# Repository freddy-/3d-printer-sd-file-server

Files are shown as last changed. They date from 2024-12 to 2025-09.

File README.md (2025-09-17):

# ESP8266 SD Card File Server For 3D Printer

This project mimics the file upload endpoint of OctoPrint allowing to send gcode from prusa slicer and saving direct to SD card.

It is based on ardyesp/ESPWebDAV and FYSETC/ESPWebDAV.
 
SD card is shared between ESP8266 (SPI) and 3d printer (SDIO) running Marlin firmware with a custom change. 

The ESP8266 control the SD Card detection pin from the 3D Printer board. When it receive a file upload it simulate a SD card removal from the 3D Printer and then initialize the SD Card in SPI mode. When the file upload is done it performs a power cycle of the SD Card, otherwise the SD Card wont work in SDIO mode.

This change in Marlin allow the SDIO lines from the SD card to be shared with the ESP8266. When the card is removed from the 3D Printer Marlin detects and disable the SDIO hardware and set these pins to input.

### 3D Printer
The tests were made using a Kingroon KP3S. This printer have a MakerBase Robin Nano clone board with a connector for a external SD board.

### Firmware update
Firmware update can be done via browser through url `<esp-ip>/update`

### Dependencies
- [ESP8266 Arduino](https://github.com/esp8266/Arduino)  version 3.1.2

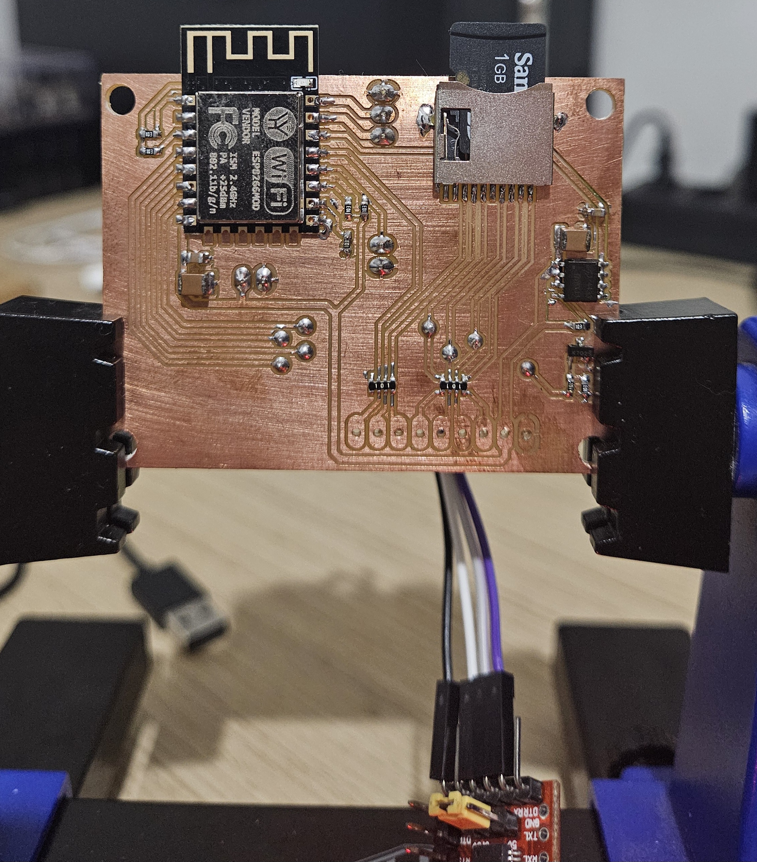
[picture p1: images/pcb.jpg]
pcb


<div style="display: flex;">
  <a href="images/printer1.jpg">
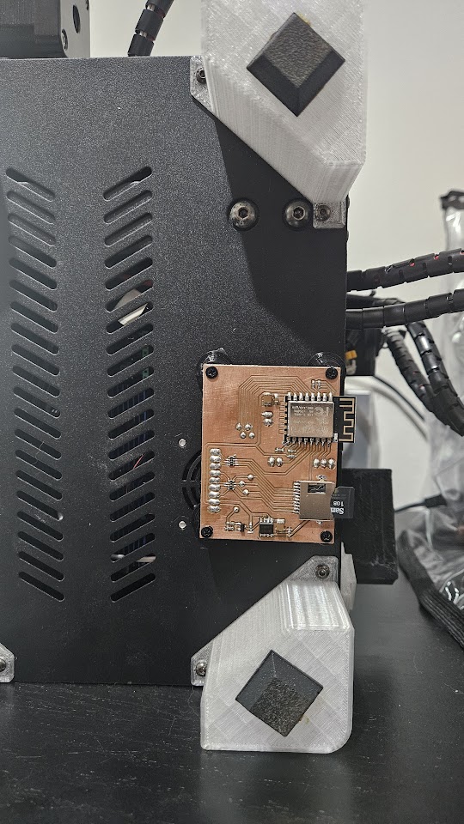
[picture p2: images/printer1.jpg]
    
  </a>
  <a href="images/printer2.jpg">
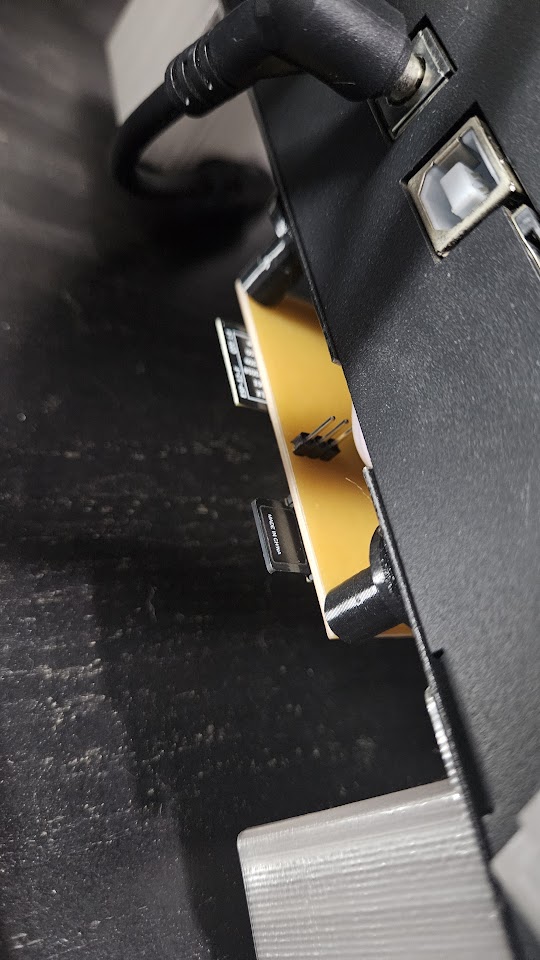
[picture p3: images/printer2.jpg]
    
  </a>
</div>

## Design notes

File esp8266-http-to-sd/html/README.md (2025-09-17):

# Convert HTML to C Array

This is based in the [ESP8266 FSBrowser](https://github.com/esp8266/Arduino/tree/master/libraries/ESP8266WebServer/examples/FSBrowser) example.

To convert a HTML file into a minified C Array run this command with the html file name without the `.html`:

```bash
./convert_html_to_c_header.sh index
```

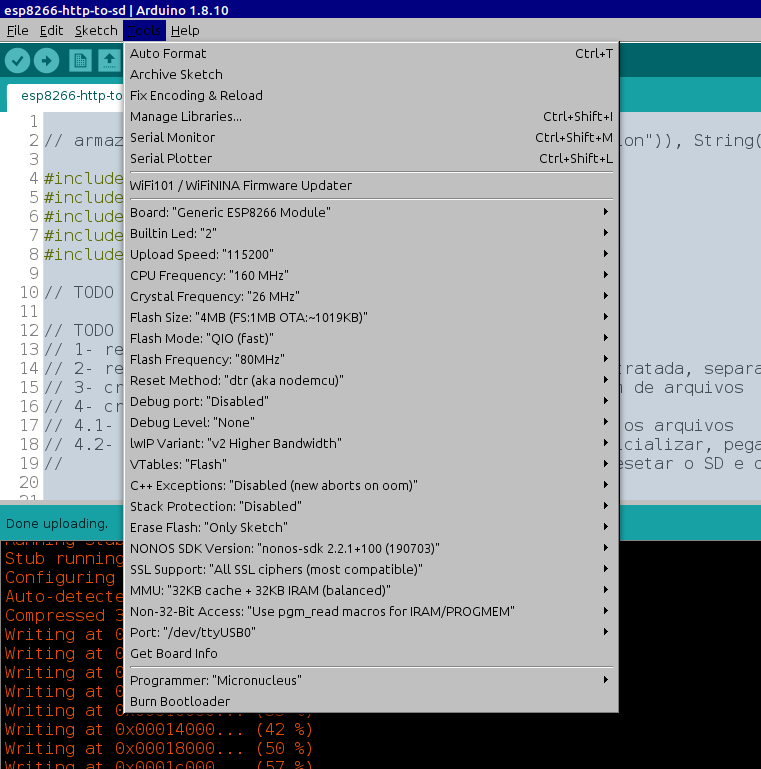
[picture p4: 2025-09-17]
esp8266-http-to-sd/arduino-config.png

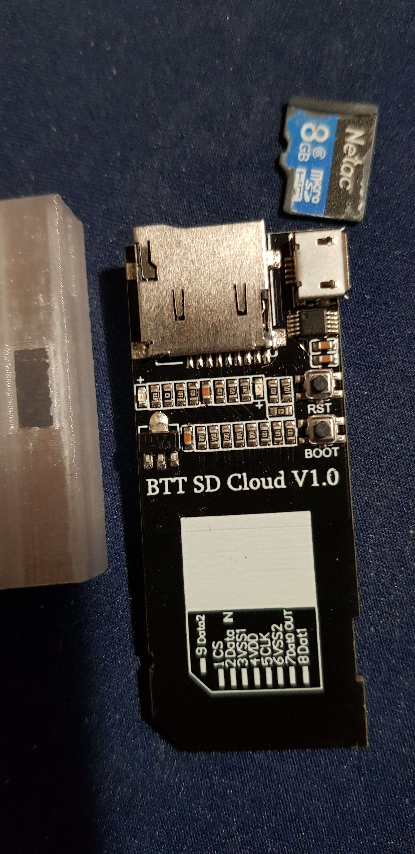
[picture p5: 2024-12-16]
esp8266-http-to-sd/99077462-14074700-25bd-11eb-9805-0963f63b4c84.jpg

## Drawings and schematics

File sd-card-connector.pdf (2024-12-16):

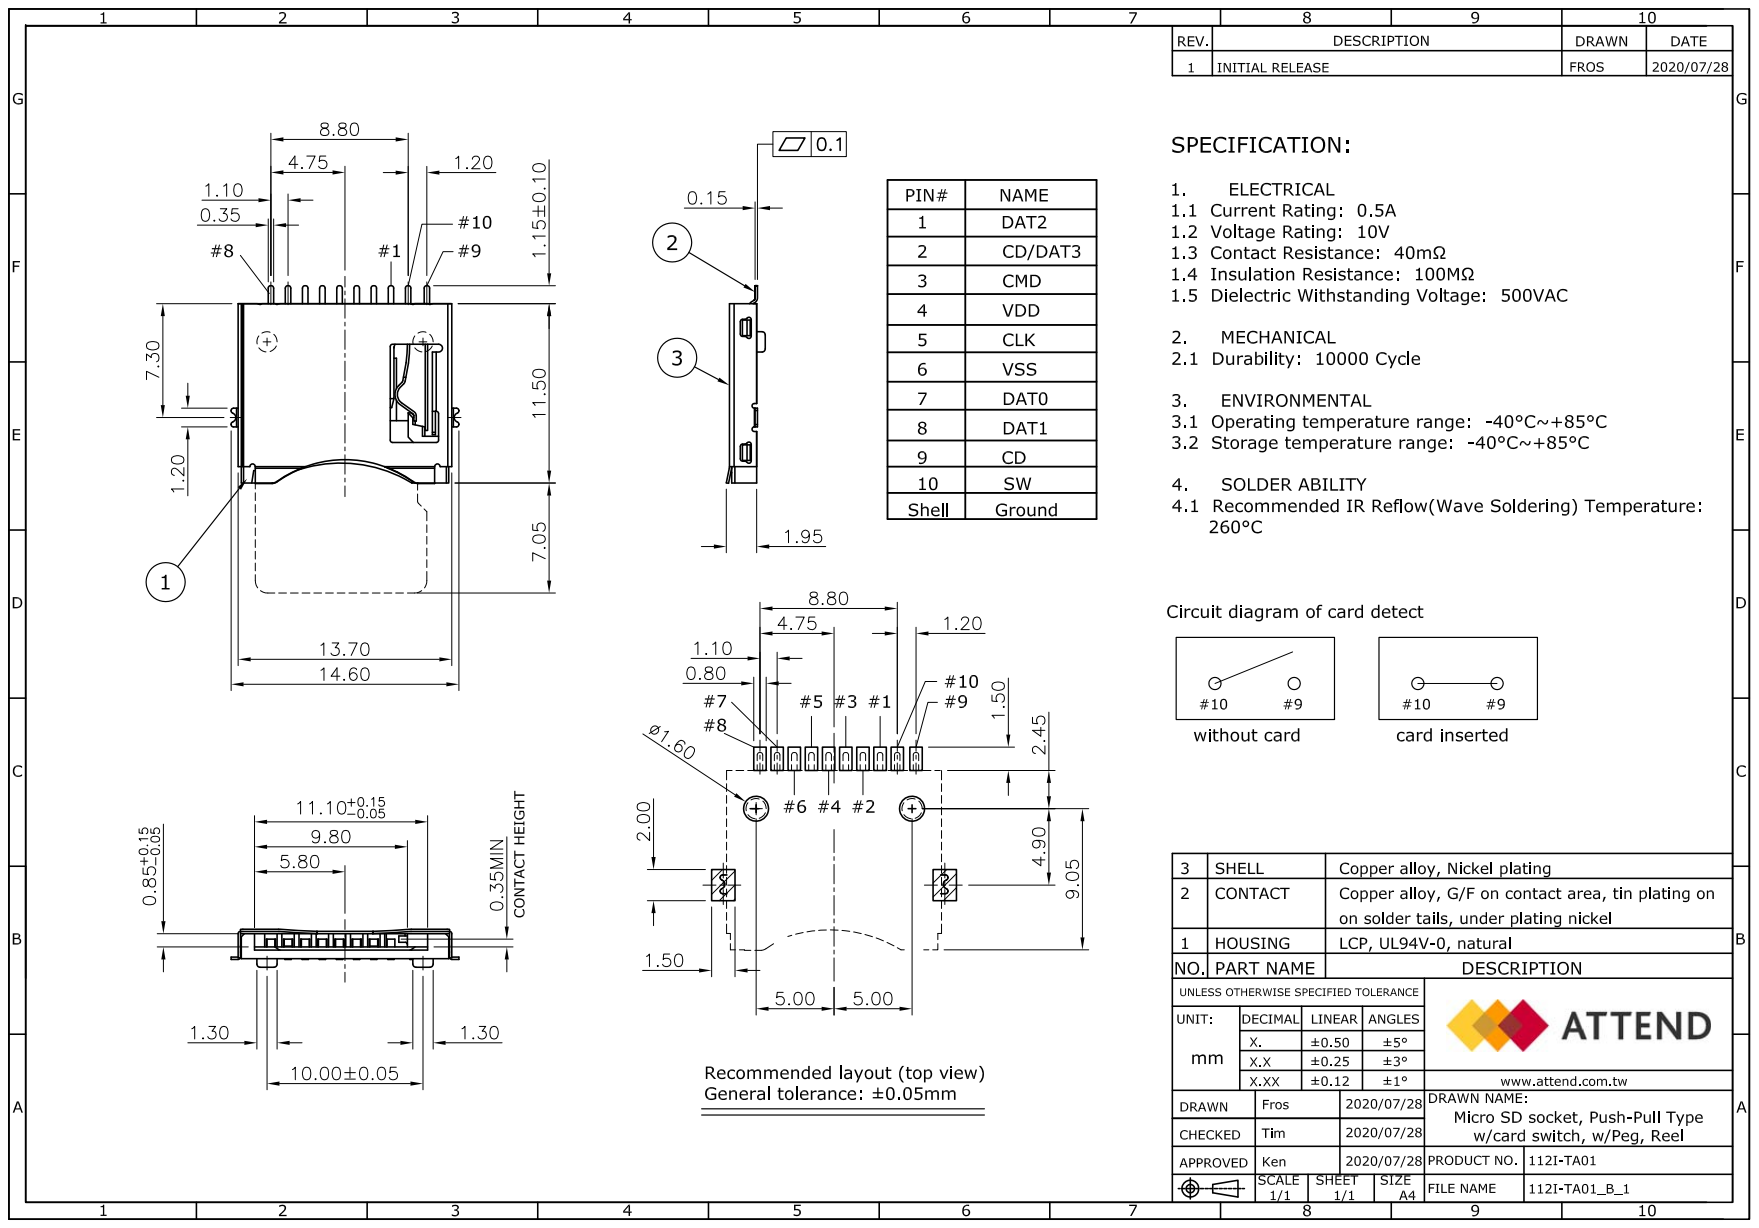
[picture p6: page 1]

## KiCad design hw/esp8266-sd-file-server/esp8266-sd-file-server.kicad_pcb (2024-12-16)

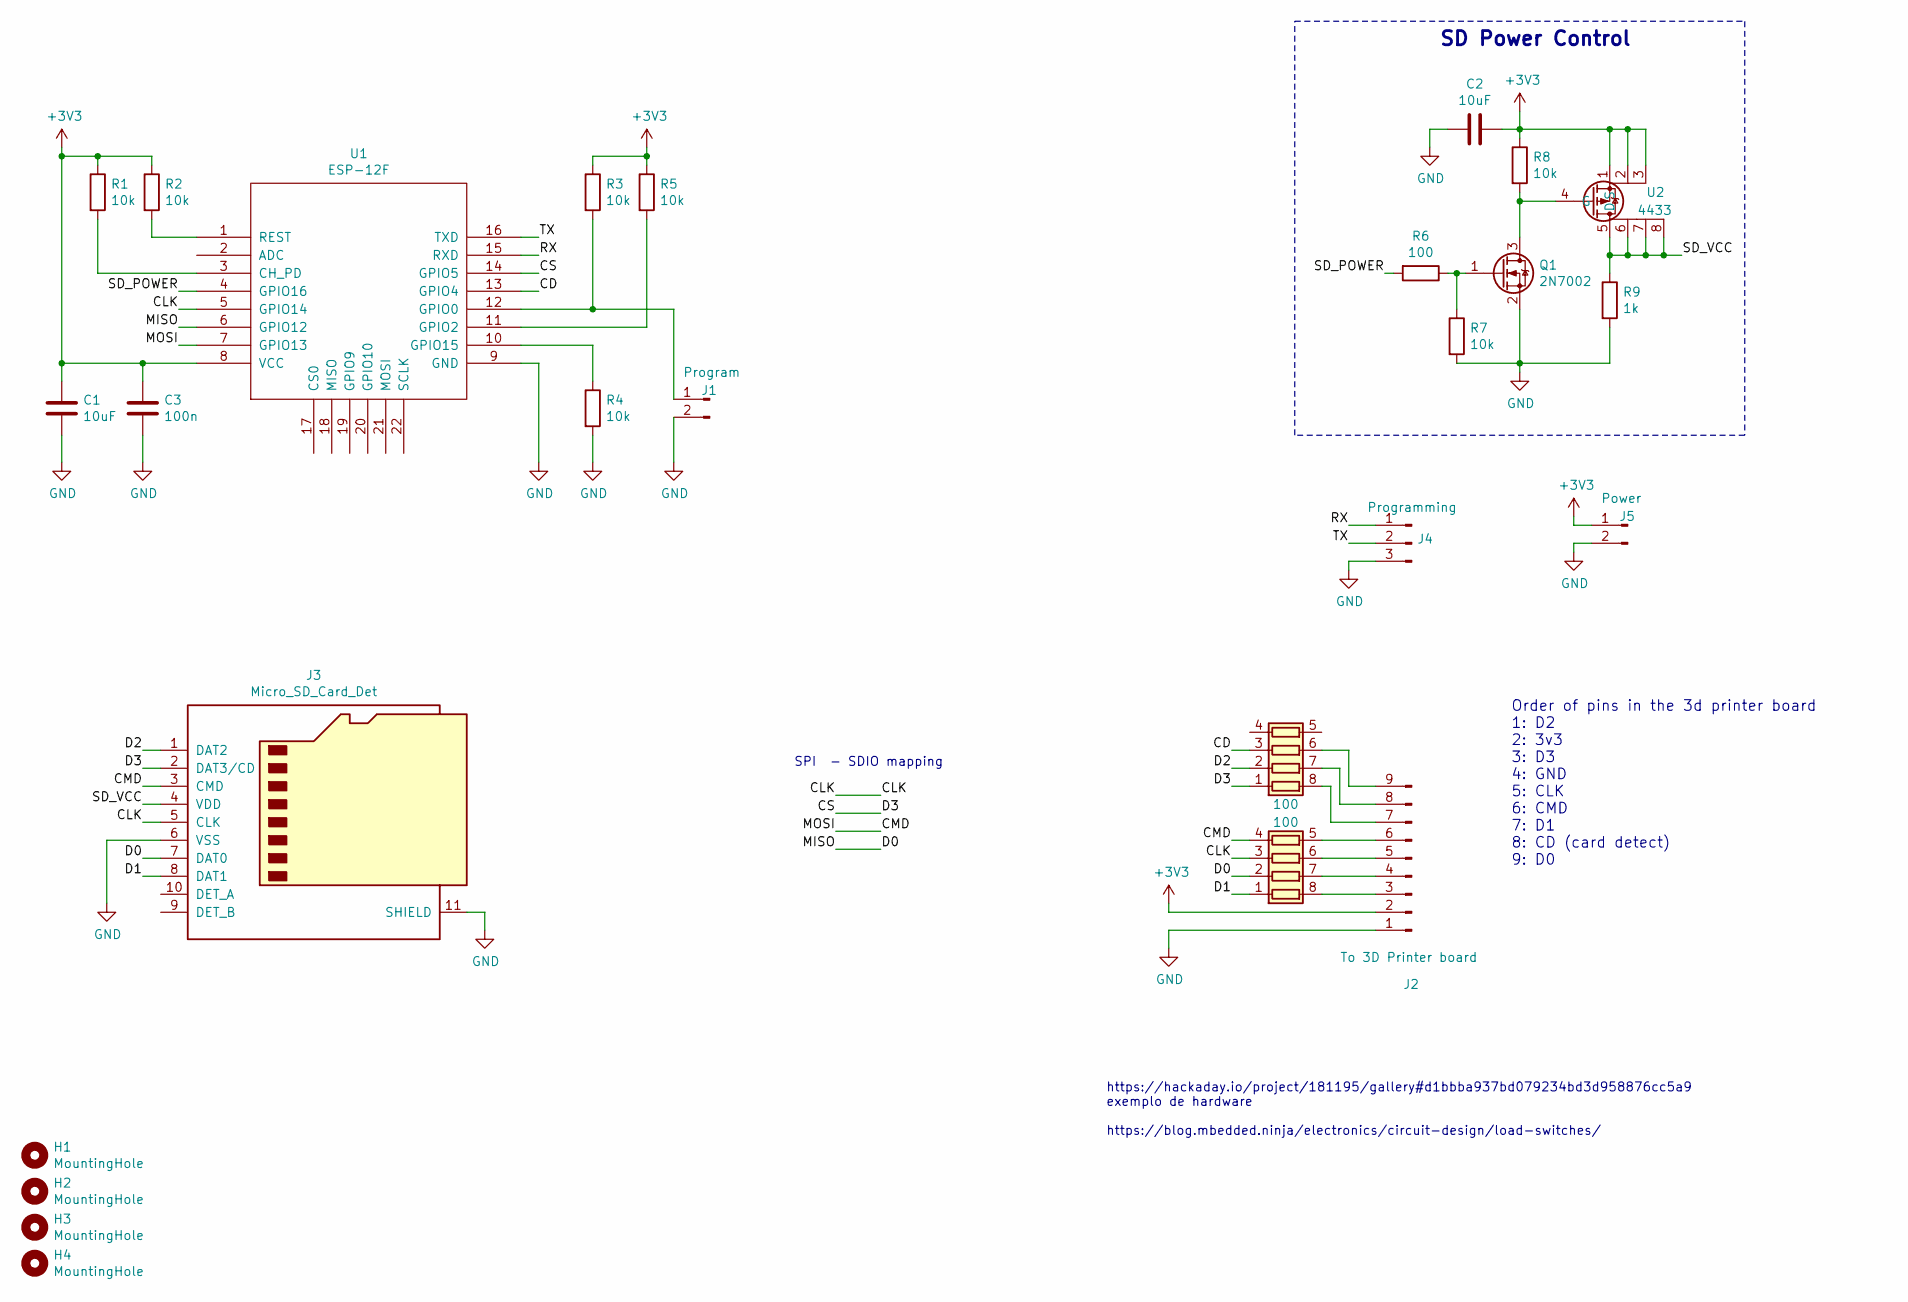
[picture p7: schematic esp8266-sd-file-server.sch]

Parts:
C1, C2: 10uF; C_1210_3225Metric_Pad1.42x2.65mm_HandSolder
C3: 100n; C_0805_2012Metric_Pad1.15x1.40mm_HandSolder
H1, H2, H3, H4: MountingHole; MountingHole_3mm
J1: Program; PinHeader_1x02_P2.54mm_Vertical
J2: To 3D Printer board; PinHeader_1x09_P2.54mm_Vertical
J3: Micro_SD_Card_Det; micro_sd
J4: Programming; PinHeader_1x03_P2.54mm_Vertical
J5: Power; PinHeader_1x02_P2.54mm_Vertical
Q1: 2N7002; SOT-23
R1, R2, R3, R4, R5, R7, R8: 10k; R_0603_1608Metric_Pad1.05x0.95mm_HandSolder
R6: 100; R_0603_1608Metric_Pad1.05x0.95mm_HandSolder
R9: 1k; R_0603_1608Metric_Pad1.05x0.95mm_HandSolder
RN1, RN2: 100; R_Array_Convex_4x0603
U1: ESP-12F; ESP-12E_SMD
U2: 4433; SOIC-8_3.9x4.9mm_P1.27mm

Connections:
+3V3: C1.2, C2.1, C3.2, J2.2, J5.1, R1.1, R2.1, R3.1, R5.1, R8.1, U1.8 (VCC), U2.1 (S), U2.2, U2.3
/CD: RN2.3 (R3.1), U1.13 (GPIO4)
/CLK: J3.5 (CLK), RN1.3 (R3.1), U1.5 (GPIO14)
/CMD: J3.3 (CMD), RN1.4 (R4.1), U1.7 (GPIO13)
/CS: J3.2 (DAT3/CD), RN2.1 (R1.1), U1.14 (GPIO5)
/D0: J3.7 (DAT0), RN1.2 (R2.1), U1.6 (GPIO12)
/D1: J3.8 (DAT1), RN1.1 (R1.1)
/D2: J3.1 (DAT2), RN2.2 (R2.1)
/RX: J4.1, U1.15 (RXD)
/SD_POWER: R6.2, U1.4 (GPIO16)
/SD_VCC: J3.4 (VDD), R9.1, U2.5 (D), U2.6, U2.7, U2.8
/TX: J4.2, U1.16 (TXD)
GND: C1.1, C2.2, C3.1, J1.2, J2.1, J3.6 (VSS), J3.11 (SHIELD), J4.3, J5.2, Q1.2 (S), R4.2, R7.2, R9.2, U1.9 (GND)
unnamed: J1.1, R3.2, U1.12 (GPIO0)
unnamed: J2.3, RN1.8 (R1.2)
unnamed: J2.4, RN1.7 (R2.2)
unnamed: J2.5, RN1.6 (R3.2)
unnamed: J2.6, RN1.5 (R4.2)
unnamed: J2.7, RN2.8 (R1.2)
unnamed: J2.8, RN2.7 (R2.2)
unnamed: J2.9, RN2.6 (R3.2)
unnamed: Q1.1 (G), R6.1, R7.1
unnamed: Q1.3 (D), R8.2, U2.4 (G)
unnamed: R1.2, U1.3 (CH_PD)
unnamed: R2.2, U1.1 (REST)
unnamed: R4.1, U1.10 (GPIO15)
unnamed: R5.2, U1.11 (GPIO2)

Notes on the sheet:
SD Power Control
https://hackaday.io/project/181195/gallery#d1bbba937bd079234bd3d958876cc5a9 exemplo de hardware https://blog.mbedded.ninja/electronics/circuit-design/load-switches/
SPI - SDIO mapping
Order of pins in the 3d printer board 1: D2 2: 3v3 3: D3 4: GND 5: CLK 6: CMD 7: D1 8: CD (card detect) 9: D0

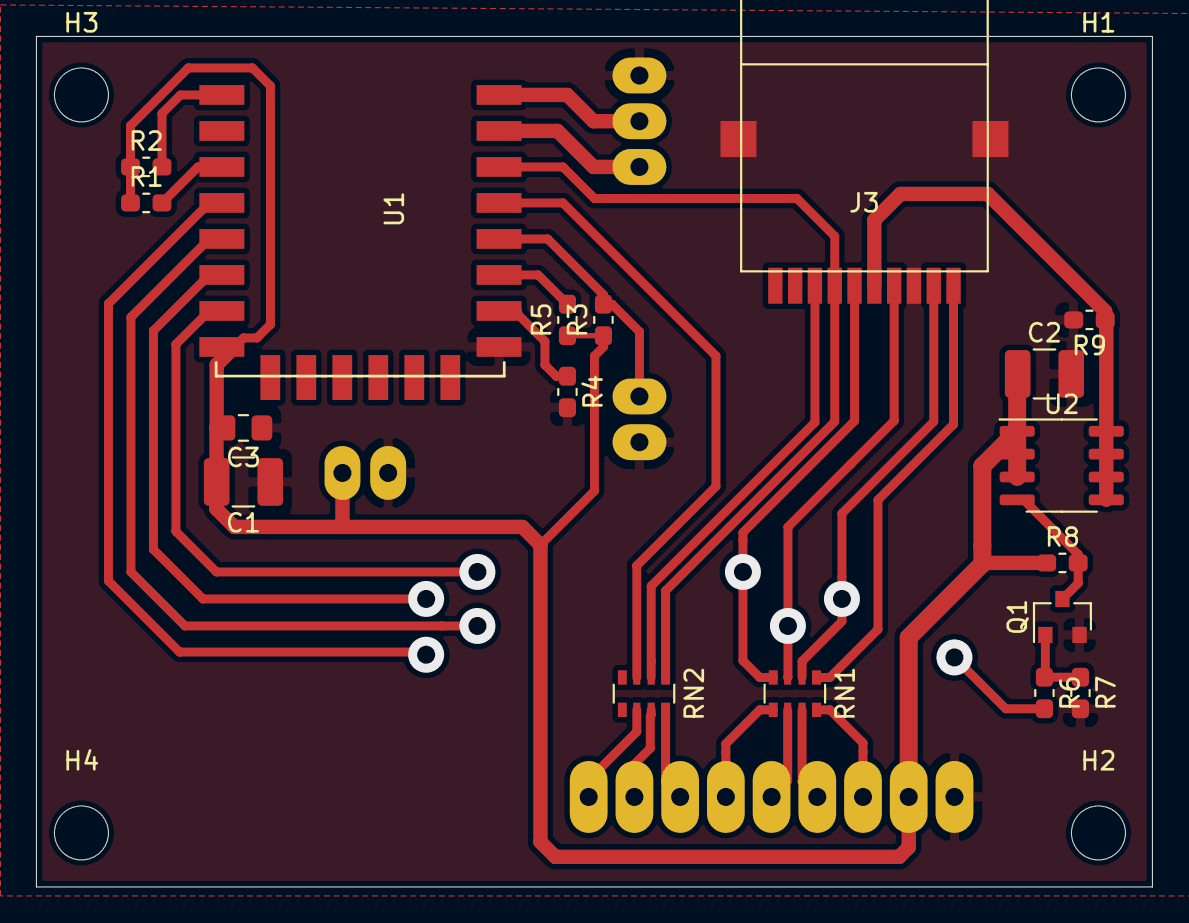
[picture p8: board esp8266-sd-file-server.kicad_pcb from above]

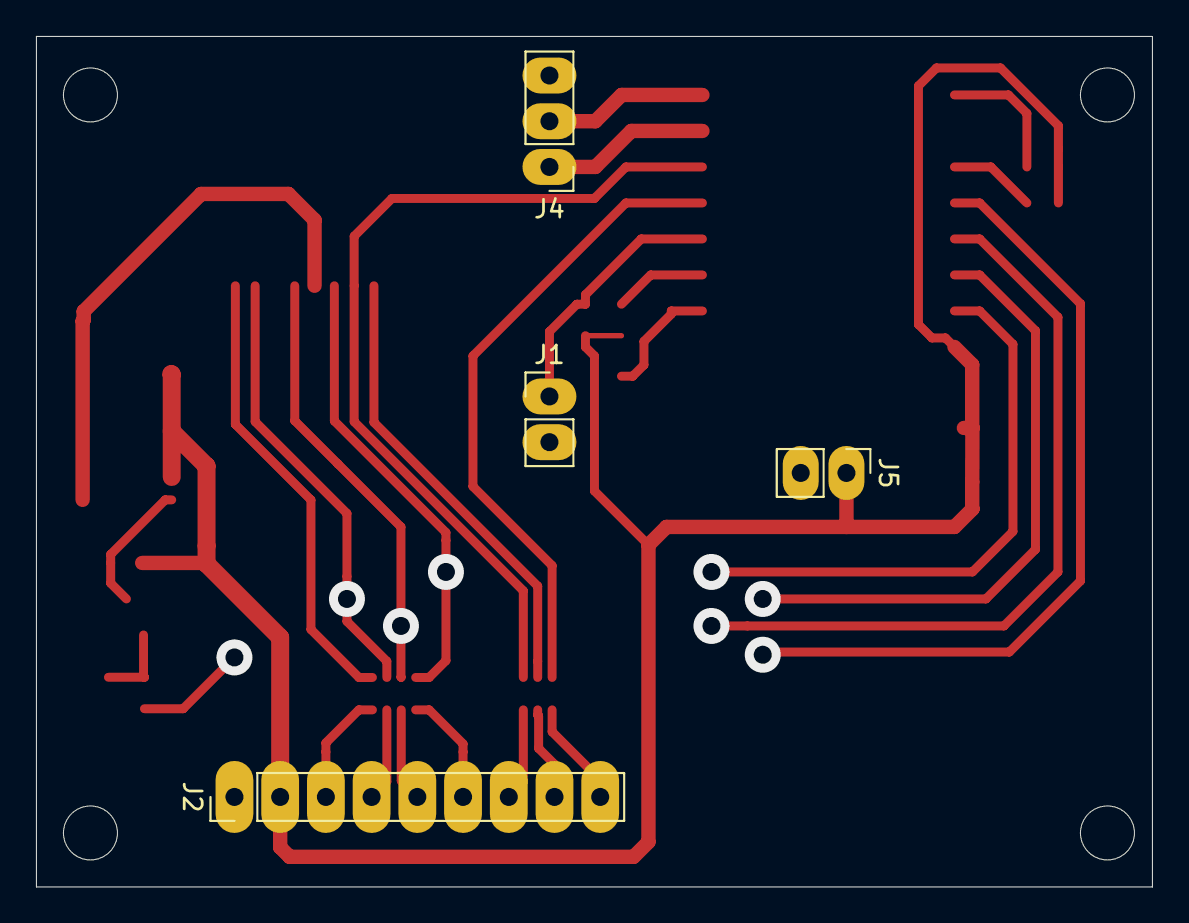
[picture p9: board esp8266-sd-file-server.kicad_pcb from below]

Board: 2 copper layers, 62.0 x 47.2 mm, 26 parts (4 on the bottom side), 27 nets.

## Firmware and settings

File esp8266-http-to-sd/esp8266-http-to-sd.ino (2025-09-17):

// armazenar string na flash sendHeader(String(F("Connection")), String(F("close")));

#include <ESP8266WiFi.h>
#include <SPI.h>
#include <SdFat.h>
#include "html/index_htm.h"
#include "html/update_htm.h"
#include "./wifi-credentials.h"
#include "custom_types.h"

// TODO usar mdns pra nao precisar de ip fixo

// TODO
// 1- renomear o index_html pra update_html
// 2- refatorar os ifs que verificam qual URL deverá ser tratada, separar em funções
// 3- criar um index_html com links para update e listagem de arquivos
// 4- criar a listagem de arquivo:
// 4.1- ao abrir a tela devera ter um botão pra consultar os arquivos
// 4.2- ao executar esta consulta, devemos pegar o sd, inicializar, pegar o tamanho total, tamanho
//      usado e listar os arquivos, em seguida retornar resetar o SD e devolver ele pro marlin


// Pins
#define SD_POWER    16 // D0
#define CS_PIN      5  // D1
#define MISO_PIN		12 // D6
#define MOSI_PIN		13 // D7
#define CLK_PIN     14 // D5
#define CD_PIN      4  // D2 - used to control sd card detection in marlin, LOW = SD inserted

// TODO get this data from sd card config.ini file
// ssid;passwd

extern const char* ssid;
extern const char* password;

// Create an instance of the server
// specify the port to listen on as an argument
WiFiServer server(80);
SdFat32 sd;
String ipAddr;
uint32_t maxSketchSpace;
const int MAX_ROUTES = 10;
RouteItem routes[MAX_ROUTES];
int numRoutes = 0;

void setup() {
  // first of all, power the SD card (it's already high at esp boot)
  pinMode(SD_POWER, OUTPUT);
  digitalWrite(SD_POWER, HIGH);

  // set MISO, MOSI, CLK, CS as input
  pinMode(MISO_PIN, INPUT); // NAO PRECISA DE RESISTOR! REMOVER 3 RESISTORES DESNECESSARIOS E COLOCAR EM PARALELEO COM OS 3 QUE SOBRAREM
  pinMode(MOSI_PIN, INPUT);
  pinMode(CLK_PIN,  INPUT);
  pinMode(CS_PIN,   INPUT);

  pinMode(CD_PIN,   OUTPUT); 
  digitalWrite(CD_PIN, LOW); // insert card into marlin


  Serial.begin(115200);
  Serial.printf("Update %d\n", Update.size());
  delay(10);

  maxSketchSpace = (ESP.getFreeSketchSpace() - 0x1000) & 0xFFFFF000;
  Serial.println(maxSketchSpace);
  
  // Connect to WiFi network
  Serial.println();
  Serial.println();
  Serial.print("Connecting to ");
  Serial.println(ssid);
  
  WiFi.mode(WIFI_STA);
  WiFi.setPhyMode(WIFI_PHY_MODE_11N);
  WiFi.begin(ssid, password);
  
  while (WiFi.status() != WL_CONNECTED) {
    delay(500);
    Serial.print(".");
  }
  Serial.println("");
  Serial.println("WiFi connected");
  
  // Start the server
  server.begin();
  Serial.println("Server started");

  // Print the IP address
  ipAddr = WiFi.localIP().toString();
  Serial.println(ipAddr);

  // Setup Web Server Routes
  addRoute("GET / HTTP",            handleIndex);
  addRoute("GET /api/version",      handleGetApiVersion);
  addRoute("POST /api/files/local", handlePostFileUploadToSdCard);
  addRoute("GET /update",           handleGetUpdateFirmware);
  addRoute("POST /update",          handlePostUpdateFirmware);
  addRoute("GET /reboot",           handleReboot);

}

void loop() {
  // Check if a client has connected
  WiFiClient client = server.available();
  if (!client) {
    return;
  }
  
  // Wait until the client sends some data
  Serial.println("\nnew client");
  int timeout_ms = 1000;
  while(!client.available() && --timeout_ms) {
    delay(1);
  }

  if (!timeout_ms) {
    Serial.println("Client timed out!");
    return;
  }
  
  // Route the request
  routeRequest(client);
}

size_t readBytesWithTimeout(WiFiClient client, uint8_t *buf, size_t bufSize, size_t numToRead) {
	int timeout_ms = 1000;
	size_t numAvailable = 0;
	
	while(((numAvailable = client.available()) < numToRead) && client.connected() && timeout_ms--) 
		delay(1);

	if(!numAvailable)
		return 0;

	return client.read(buf, bufSize);
}

void handleWriteError(WiFiClient client, String message, File32 *file)	{
// ------------------------
	// close this file
	file->close();
	// delete the wrile being written
	//sd.remove(uri.c_str());
  Serial.print("Write Error: ");
  Serial.println(message);
  client.print("HTTP/1.1 400 Bad Request\r\n\r\n");
  client.flush();

  releaseSdBus();
  digitalWrite(CD_PIN, LOW);
}

void handleIndex(WiFiClient client) {
  returnStaticHtmlPage(client, index_htm_gz, index_htm_gz_len);
}

void handleGetApiVersion(WiFiClient client) {
  client.print(String(F("HTTP/1.1 200 OK\r\n\r\n{\"api\":\"0.1\",\"text\":\"OctoPrint 1.10.1\"}")));
  client.flush();
}

void handlePostFileUploadToSdCard(WiFiClient client) {
  String req;
  String fileName = "";
  size_t fileSize = 0;
  uint8_t boundaryLength = 0;

  // extract length and file name from headers
  while(1) {
    req = client.readStringUntil('\r');
    client.readStringUntil('\n');

    if(req.indexOf("Content-Length") != -1) {
      int headerDiv = req.indexOf(':');
      fileSize = req.substring(headerDiv + 2).toInt();
      continue;
    }

    int idxBoundary = req.indexOf("boundary");
    if (idxBoundary != -1) {
      boundaryLength = req.substring(idxBoundary + 9, req.length()).length();
      continue;
    }
    
    int idxFileName = req.indexOf("filename");
    if (idxFileName != -1) {
      fileName = req.substring(idxFileName + 10, req.length() - 1);
      break;
    }
  }

  if (fileSize == 0 || fileName.length() == 0) {
    Serial.println("Invalid request");
    client.print("HTTP/1.1 400 Bad Request\r\n\r\n");
    client.flush();
    return;
  }

  Serial.print("File: ");
  Serial.println(fileName);
  Serial.print("Size: ");
  Serial.println(fileSize);

  // pula o content type que restou da request
  client.readStringUntil('\r');
  client.readStringUntil('\n');

  // remove card from marlin and wait a little bit
  digitalWrite(CD_PIN, HIGH);
  delay(1000);

  takeSdBus();

  // SD init
  if (sd.begin(SdSpiConfig(CS_PIN, DEDICATED_SPI, SPI_FULL_SPEED))) { //SPI_DIV3_SPEED SPI_FULL_SPEED SPI_HALF_SPEED
    Serial.println("SD init ok");
  } else {
    Serial.println("SD init fail!!!!!");
    return;
  }  

  // receber o restante do request
  File32 file;
  size_t numRemaining = fileSize;
  const size_t WRITE_BLOCK_CONST = 512;
  uint8_t buf[WRITE_BLOCK_CONST];

  size_t contBlocks = (fileSize/WRITE_BLOCK_CONST + 1);
  uint32_t bgnBlock, endBlock;

  // remove old file if exists
  if (sd.exists(fileName.c_str())) {
    Serial.println("File exists, removing...");
    sd.remove(fileName.c_str());
  }

  if (!file.open(fileName.c_str(), O_RDWR | O_CREAT)) {
    return handleWriteError(client, "open file failed", &file);
  }
  if (!file.preAllocate(fileSize)) {
    return handleWriteError(client, "preAllocate failed", &file);
  }

  uint32_t time = millis();
  while(numRemaining > 0)	{
    size_t numToRead = (numRemaining > WRITE_BLOCK_CONST) ? WRITE_BLOCK_CONST : numRemaining;
    size_t numRead = readBytesWithTimeout(client, buf, sizeof(buf), numToRead);

    if(numRead == 0)
      break;

    if (file.write(buf, numRead) != numRead) {
      return handleWriteError(client, "Write data failed", &file);
    }

    numRemaining -= numRead;
  }
  time = millis() - time;
  Serial.printf("Speed: %d, time %d \n", fileSize/time, time);

  if (!file.sync()) {
    return handleWriteError(client, "File Sync failed", &file);
  }

  if (!file.truncate(fileSize - numRemaining - boundaryLength - 6)) {
    return handleWriteError(client, "Unable to truncate the file", &file);
  }

  file.close();

  Serial.println("File created!");
  
  client.print("HTTP/1.1 200 OK\r\n\r\n");
  client.flush();

  releaseSdBus();
  
  // do a power off in the SD card
  digitalWrite(SD_POWER, LOW);
  delay(200);

  // then power it up again
  digitalWrite(SD_POWER, HIGH);
  delay(200);

  // and then insert into marlin
  digitalWrite(CD_PIN, LOW);
}

void handleGetUpdateFirmware(WiFiClient client) {
  returnStaticHtmlPage(client, update_htm_gz, update_htm_gz_len);
}

void handlePostUpdateFirmware(WiFiClient client) {
  // curl -F "image=@esp8266-http-to-sd.ino.generic.bin" 192.168.0.70/update

  String req;
  size_t fileSize = 0;
  while(1) {
    req = client.readStringUntil('\n');

    if(req.indexOf("Content-Disposition: form-data; name=\"size\"") != -1) {
      client.readStringUntil('\n');       // read empty line
      req = client.readStringUntil('\n'); // read the value
      fileSize = req.toInt();
      continue;
    }

    if(req.indexOf("Content-Disposition: form-data; name=\"update\"") != -1) {
      client.readStringUntil('\n');       // read content type line
      client.readStringUntil('\n');       // read empty
      break;
    }
  }
  
  Serial.setDebugOutput(true);  
  if (!Update.begin(maxSketchSpace)) {    // start firmware update
    Serial.println("Erro ao iniciar update");
    Update.printError(Serial);
  }

  size_t numRemaining = fileSize;
  uint8_t buffer[2048];
  while(numRemaining > 0)	{
    size_t numToRead = (numRemaining > 2048) ? 2048 : numRemaining;
    size_t numRead = readBytesWithTimeout(client, buffer, numToRead, numToRead);

    if(numRead == 0) break;

    if (Update.write(buffer, numRead) != numRead) {
      Update.printError(Serial);
    }

    numRemaining -= numRead;
  }

  if (Update.end(true)) { // true to set the size to the current progress
    Serial.printf("Update Success: %u\nRebooting...\n", fileSize);
  } else {
    Update.printError(Serial);
  }
  Serial.setDebugOutput(false);

  client.print("HTTP/1.1 302 Found\r\n");
  client.print("Location: http://");
  client.print(ipAddr);
  client.print("/update?reboot=true\r\n\r\n");
  client.flush();
}

void handleReboot(WiFiClient client) {
  client.print("HTTP/1.1 200 ok\r\n\r\n");
  client.flush();
  ESP.restart();
}

void handleNotFound(WiFiClient client) {
  Serial.println("invalid request");
  client.print("HTTP/1.1 404 Not Found\r\n\r\n");
  client.flush();
}

void returnStaticHtmlPage(WiFiClient client, unsigned char* content, unsigned int length) {
  client.print("HTTP/1.1 200 OK\r\n");
  client.print("Content-Encoding:gzip\r\n");
  client.print("Content-Type:text/html\r\n\r\n");
  client.write(content, length);
  client.flush();
}

void addRoute(const char* path, RouteHandlerFunction handler) {
  if (numRoutes < MAX_ROUTES) {
    routes[numRoutes].path = path;
    routes[numRoutes].handler = handler;
    numRoutes++;
  } else {
    Serial.println("Erro: Numero maximo de rotas atingido!");
  }
}

void routeRequest(WiFiClient client) {
  // Read the first line of the request
  String req = client.readStringUntil('\r');
  client.readStringUntil('\n');
  Serial.println(req);

  const char* requestStr = req.c_str();

  for (int i = 0; i < numRoutes; i++) {
    if (strstr(requestStr, routes[i].path) != NULL) {
      routes[i].handler(client);
      return;
    }
  }

  handleNotFound(client);
}

void takeSdBus() {
  pinMode(MISO_PIN, SPECIAL);
  pinMode(MOSI_PIN, SPECIAL);
  pinMode(CLK_PIN,  SPECIAL);
  pinMode(CS_PIN,   OUTPUT);
}

void releaseSdBus() {
  pinMode(MISO_PIN, INPUT);
  pinMode(MOSI_PIN, INPUT);
  pinMode(CLK_PIN,  INPUT);
  pinMode(CS_PIN,   INPUT);
}
